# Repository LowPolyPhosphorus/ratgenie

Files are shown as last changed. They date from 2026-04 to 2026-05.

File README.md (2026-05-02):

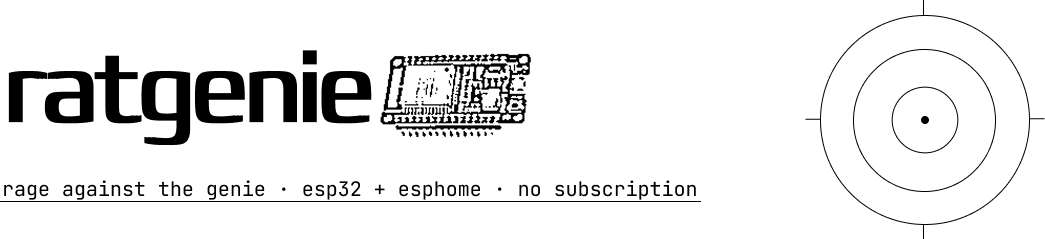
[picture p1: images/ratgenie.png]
ratgenie

 
# ratgenie
ratgenie, my solution to the insufferable thing known as a garage door opener. (specifically, Genie/MyQ/Chamberlain/LiftMaster/Raynor/Craftsman/Clicker garage door openers) similar to the ratgdo (rage against the garage door opener) the ratgenie will fix hopefully at least the MachForce Genie Garage Door Opener (new name, ratmfggdo, rolls off the tongue doesn't it?)

## what is this?
ratgenie is a locally controlled, no subscription, no cloud, no nonsense garage door controller built on an ESP32-WROOM. it wires directly into your garage door opener's wall button terminals and gives you full open/close/status control through Home Assistant over WiFi via ESPHome. no MyQ account. no Aladdin Connect. no $5/month to open your own garage door.

## why does this exist?
because Genie/Chamberlain decided that you need a paid subscription to open your own garage door with your own phone on your own wifi network. the MachForce Connect has Aladdin Connect built in, which used to work fine, then stopped pairing after a new motor install and the only fix was apparently paying for a subscription. ratgenie is the fix.

inspired by [ratgdo](https://github.com/PaulWieland/ratgdo) by Paul Wieland, which does the same thing for Security+ 2.0 Chamberlain/LiftMaster openers. ratgenie targets Genie's dry contact interface since the MachForce doesn't use Security+ 2.0.

## what does it do?
- opens and closes your garage door from Home Assistant
- detects door open/closed state using an HC-SR04 ultrasonic sensor mounted on the ceiling (soon to be replaced by ESP32 and MCU-6050 project)
- triggers the door by momentarily shorting the wall button terminals through a relay, exactly like pressing the button yourself
- runs on ESPHome, so Home Assistant autodiscovers it over MQTT with zero configuration

## hardware
- ESP32-WROOM
- HC-SR04 ultrasonic distance sensor
- 5V single channel optocoupler relay module
- some wire

## bill of materials
| part | quantity | link |
|---|---|---|
| ESP32-WROOM | 1 | owned |
| HC-SR04 ultrasonic sensor | 1 | owned |
| 5V single channel optocoupler relay module | 1 | [aliexpress](https://www.aliexpress.us/item/3256806393437087.html) |

## tested on
- Genie MachForce Connect Model 4063-TNMSV

## not tested on
literally everything else. if you make it and it works on your opener, open an issue and let me know and i'll add it to the list.

## credits
- [ratgdo](https://github.com/PaulWieland/ratgdo) by Paul Wieland for the concept and inspiration
- [ESPHome](https://esphome.io/) for making this not a nightmare to implement
## Gallery






> ^^ your physical button should look like this in the back for this to work (two screw posts) ^^




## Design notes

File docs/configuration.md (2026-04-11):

# Configuration

All configuration is done through `firmware/ratgenie.yaml` and `firmware/secrets.yaml`.

## secrets.yaml

| Key | Description |
|-----|---|
| `wifi_ssid` | Your WiFi network name |
| `wifi_password` | Your WiFi password |
| `api_encryption_key` | Base64 encryption key for Home Assistant API |
| `ota_password` | Password for over the air firmware updates |
| `fallback_password` | Password for the fallback hotspot if WiFi fails |

## GPIO Pins

| Pin | Function |
|-----|---|
| GPIO13 | HC-SR04 trigger |
| GPIO12 | HC-SR04 echo |
| GPIO26 | Relay control |
| GPIO2 | Status LED |

These can be changed in `ratgenie.yaml` if your wiring differs.

## Distance Threshold

The ultrasonic sensor determines door state based on a distance threshold set in the `on_value` block:

```yaml
sensor.in_range:
  id: garage_distance
  above: 1.0
```

`above: 1.0` means anything over 1 meter is considered open. Adjust this based on your ceiling height. Mount the sensor on the ceiling pointing down at the door panel when closed the door will be close to the sensor, when open the sensor will see all the way to the floor.

## Relay Pulse Length

The relay closes for 500ms by default to simulate a button press:

```yaml
- switch.turn_on: door_relay
- delay: 500ms
- switch.turn_off: door_relay
```

If your opener does not trigger reliably, try increasing this to 750ms or 1000ms.

## Status LED

The status LED on GPIO2 blinks every 5 seconds when WiFi is connected and stays solid when disconnected. The check interval can be changed here:

```yaml
interval:
  - interval: 5s
```

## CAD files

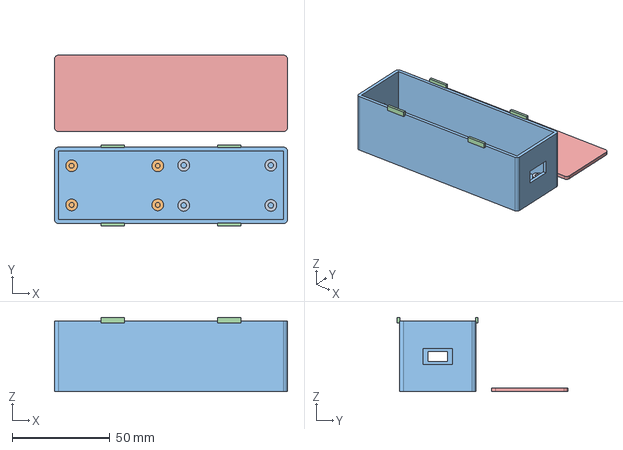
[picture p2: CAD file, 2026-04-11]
models/ratgenie.step
119.0 x 87.2 x 38.0 mm

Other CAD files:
models/ratgenie.f3d

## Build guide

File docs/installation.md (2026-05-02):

# Installation

## Requirements

- ESP32-WROOM
- ESPHome CLI (`pip install esphome`)
- Home Assistant with ESPHome integration

## Flashing

1. Clone the repo
2. Copy `firmware/secrets.yaml.example` to `firmware/secrets.yaml` and fill in your WiFi credentials and keys
3. Generate an API encryption key by running this in PowerShell:
```powershell
   [Convert]::ToBase64String((1..32 | ForEach-Object { [byte](Get-Random -Max 256) }))
```
4. Run `esphome run firmware/ratgenie.yaml` from the repo root
5. Select the COM port when prompted

## Home Assistant

Once flashed and on your network, Home Assistant will autodiscover ratgenie automatically. Go to Settings > Devices & Services and accept the ESPHome notification. Enter your API encryption key from secrets.yaml when prompted.

## Wiring

See [wiring diagram](../images/wiring.svg) for full wiring details. The relay COM and NO terminals wire in parallel with your existing wall button terminals on the opener.

## Notes

- PlatformIO cannot handle spaces in file paths on Windows. Keep the firmware folder at a path with no spaces like `C:\firmware`
- GPIO12 and GPIO2 are strapping pins and will show warnings during compile, this is expected and safe to ignore
- The ultrasonic sensor is optional for v1, the cover entity uses optimistic mode by default
- A custom built tilt and acceleration sensor for direct integration into the ratgenie is in the works! (ultrasonic sensor may be deprecated because it is overly complicated to wire it all the way to the door from the button)

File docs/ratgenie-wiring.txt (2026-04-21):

ESP32-WROOM          HC-SR04
-----------          -------
3V3  ----------->   VCC
GND  ----------->   GND
D13  ----------->   TRIG
D12  ----------->   ECHO

ESP32-WROOM          RELAY MODULE
-----------          ------------
VIN  ----------->   DC+
GND  ----------->   DC-
D26  ----------->   IN

RELAY MODULE         GARAGE OPENER
------------         -------------
COM  ----------->   WALL BUTTON TERMINAL 1
NO   ----------->   WALL BUTTON TERMINAL 2

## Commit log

2026-04-10 Add wiring instructions for ESP32 and components
2026-04-10 Revise bill of materials format in README
    Updated the bill of materials section with a table format and added a link for the relay module.
2026-04-10 Update ratgenie.yaml for OTA and status LED
    Refactor OTA encryption and add status LED functionality.
2026-04-11 Added Source f360 files and STEP
    [ratgenie.f3d, ratgenie.step]
2026-04-11 Delete ultrasonic sensor for garage door detection
    Removed ultrasonic sensor configuration for garage door.
2026-04-11 Create installation.md for ESP32-WROOM setup
    Added installation instructions for ESP32-WROOM with ESPHome.
2026-04-11 (un)Implement ultrasonic sensor for garage door status
    Added ultrasonic sensor for garage door distance monitoring.
2026-04-11 Fix formatting of door_relay switch off command
2026-04-11 Add configuration documentation for firmware setup
    Added detailed configuration instructions for firmware setup, including secrets, GPIO pin assignments, distance threshold settings, relay pulse length, and status LED behavior.
2026-04-21 Fix wiring instructions formatting in ratgenie file
2026-05-02 Update installation instructions with sensor info
    Added note about custom tilt and acceleration sensor development.
2026-05-02 Enhance README with sensor upgrade information
    Updated functionality description and future plans for the project.
